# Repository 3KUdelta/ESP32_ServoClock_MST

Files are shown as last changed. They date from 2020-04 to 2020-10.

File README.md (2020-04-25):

# ESP32 ServoClock

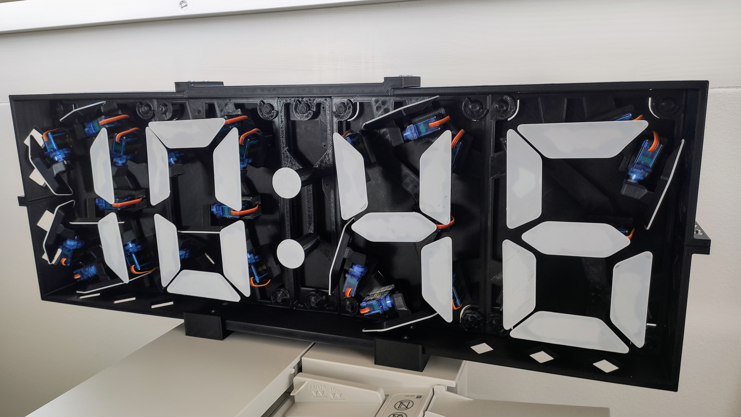
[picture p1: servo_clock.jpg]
ESP32 Servo Clock (https://github.com/3KUdelta/ESP32_ServoClock_MST)
\
Arduino code for digital clock, 3D printed inspired by www.otvinta.com, https://www.thingiverse.com/thing:3266949.
I added some thin back covers to hide the cables and added two feet to give a safe stand. These files are here: https://www.thingiverse.com/thing:4313748  

Author of the code: Jordi Ginjaume. Excellent code Jordi! It inspired me to do the thing with Arduino. Original Version 20190118 (his code and case can be found here: https://www.thingiverse.com/thing:3375870) 

Modified for use with an ESP32 wihtout RTC, just calling NTP all 12 hours over WiFi using the following hardware:

1 ESP32 programmed with Arduino\
2 PCA9685 chaining servo drivers, set solder blob on A0 on the second board for digits 3 and 4\
NTP call via WiFi\
28 SG90 servos

Important: keep sequence with servos plugging into PCA9685:\
first digit: 0-6, leave 7 blank\
second digit: 8-14, leave 15 blank\
repeat on second board for third and forth digit

PIN Connections on ESP32\
21 -- SLA\
22 -- SLC\
 0 -- OA
 
I inserted a switch to turn off the power to the PC9685 for programming purposes.

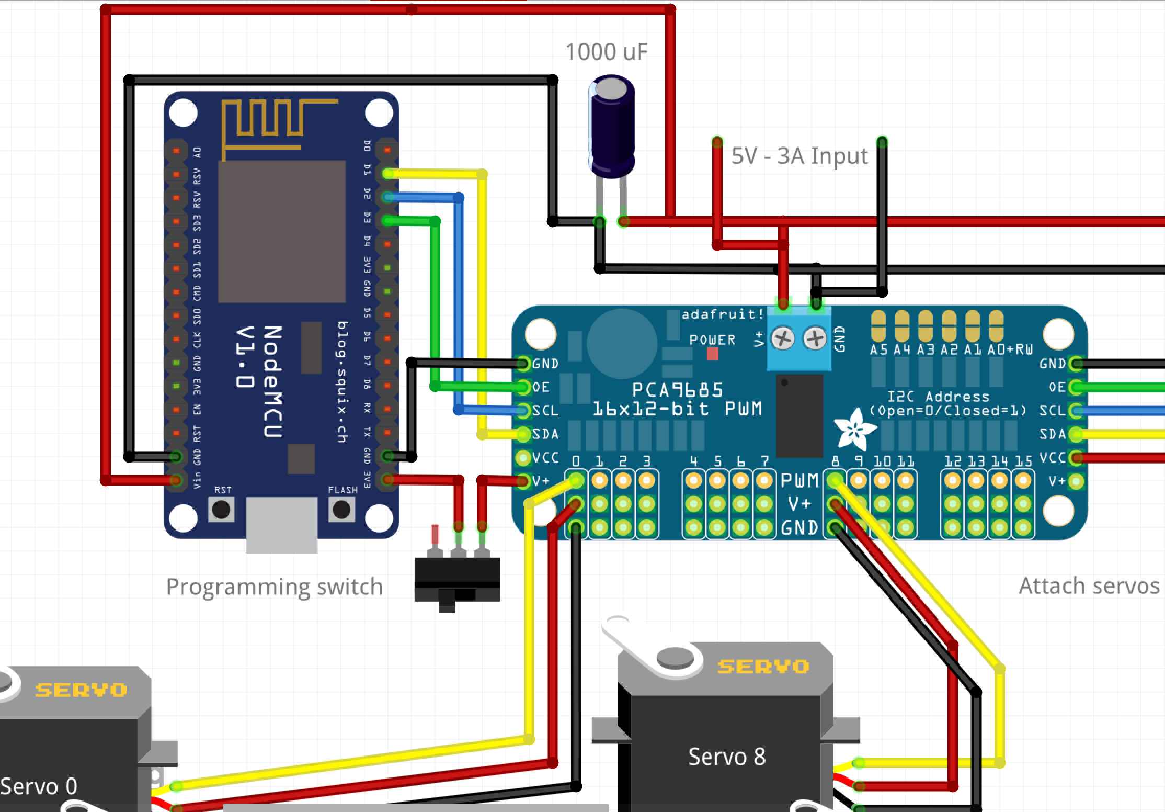
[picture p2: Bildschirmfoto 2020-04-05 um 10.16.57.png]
(https://github.com/3KUdelta/ESP32_ServoClock_MST)


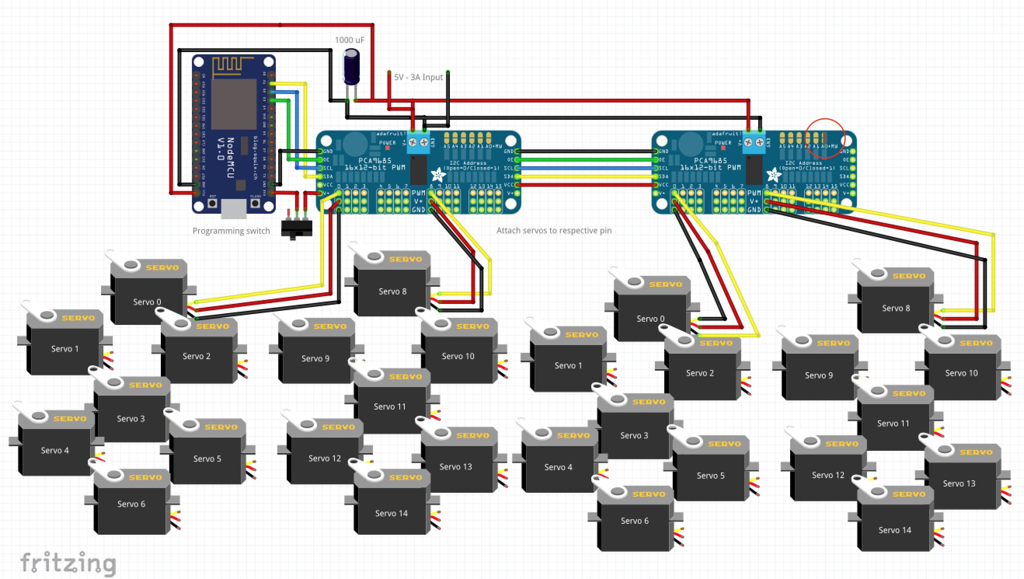
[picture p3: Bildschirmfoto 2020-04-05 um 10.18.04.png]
(https://github.com/3KUdelta/ESP32_ServoClock_MST)


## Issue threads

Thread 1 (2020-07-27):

Issues with Sketch

BzowK, 2020-07-27:
Good Morning!

I choose to use your build over the  as it's a cheaper option which seems to work just as well.  Unfortunately, I'm having two issues with your code...

## Issue 1 - 'resetFunc' was not declared in this scope ##

When attempting to verify just the original sketch you posted in IDE, I get the error above.  I added the following line above the function it's within and it verified afterwards.  Commenting out the line also verifies it, but sure it's there for a reason :)  Bringing it up as don't know if related to the 2nd issue.

    void(* resetFunc) (void) = 0; //declare reset function @ address 0

## Issue 2 - Sketch Not Working *(wdt reset)* ##
Once the above issue was addressed, I uploaded it to an NodeMCU and opened Serial Monitor.  Once up, the following was echoed and repeated every few seconds:

     ets Jan  8 2013,rst cause:4, boot mode:(3,6)
    wdt reset
    load 0x4010f000, len 1392, room 16
    tail 0
    chksum 0xd0
    csum 0xd0
    v3d128e5c
    ~ld

I've researched for at least an hour so far and found that its a watchdog reset, but don't know how to resolve it.  If it makes a difference, I have nothing connected to NodeMCU pins - it's just plugged into the PC via USB.  Some of the suggestions mention code issues, reducing long delays, & to pin assignments being incorrect.  Was hoping you could provide suggestions if not replicate.

*To note, the exact hardware I'm using is a KeeYees 3pcs ESP8266 NodeMCU CP2102 ESP-12E - a model I've never had issues with before and the pins match the ones in your diagram.*

Any suggestions or thoughts?  Thanks!

BzowK, 2020-07-27:
Think I got it working (I hope).  Basically replaced using the WiFi.h library with ESP8266WiFi.h then changed a couple other things to match.  Hopefully servo stuff works, too :)  Thanks

3KUdelta, 2020-07-27:
Hi, happy to see that it works.

Closed 2020-07-27.

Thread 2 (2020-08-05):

Servo Alignment / 12=00? / Wiring

BzowK, 2020-08-05:
Good Day, Again -

I've got two issues I've spent time trying to resolve without luck - hoping you can help...

**Servo Alignment**
So I finally got everything put together  and seemingly the sketch working, but when I powered it up, most of the segments (which I fortunately hadn't screwed in yet) went flying as it rotated them all over the place.  I added serial prints into part of the sketch so I could see which numbers it was trying to display, reattached the segments, then reset; but many went flying again :(  Not sure what the opening sequence is, but how do you suggest I proceed?

**12 Hour Clock**
I live in the US and (if I did it correctly) the serial prints are showing "00:45" for "12:45."  When not in a "12" hour, it outputs correctly.  Is there an easy code change to adjust this?  Note: The only changes I made to the time in the sketch were to define "TZ" as "6" and "UTC_OFFSET - TZ" to subtract 6 hours from the TZ as I'm Central time (US).  Here's my current sketch minus SSID/Password...
[ServoClockGen.ino.txt](https://github.com/3KUdelta/ESP32_ServoClock_MST/files/5030179/ServoClockGen.ino.txt)

**Wiring**
When initially hooking everything up, I couldn't get it to work at all.  I eventually found this post that the SCL & SDA wires should be hooked up in reverse to what your diagram showed.  Once I swapped them, it started to (theoretically) work.  I made a new Fritzing image which I pasted below as an example of what worked for me.

Any suggestions would be appreciated - Thanks!

**UPDATE**
I think I got the first one set where I can get the segments close to correct.  Not sure in sketch how to fine tune each, though.

3KUdelta, 2020-08-08:
Hi
I hope I can help you with your questions:
Servo Alignment, please use this part of the code:
`const int servofinetune [4] [7] = {      // pulse to add to servopulse for fine tunning of each individual servo
  { -25, 0, 0, 10, -30, 0, -20},
  {0, -20, 0, -10, -55, -5, 30},
  {0, -20, -15, 0, 0, 0, 0},
  {20, 20, -10, 0, 10, -10, 10}
};`

Each group represents one digit with the corresponding 7 servos. E.g. {servo0, servo1, ... }. The initial sequence puts all servos to ON. Then unplug the power. Observe the state of the servos and put a correction factor for each servo. For my build I had to correct the first servo -25. It was overshooting. You need to try this out a several times.

Time Zone and 12 hour display:
Unfortunately for you,  the code was built for European usage and automatic calculation of DST for Europe. The settings for your time zone in general are fine. The DST is an extra calculation. Therefore your changes need to consider exchanging the rules for the daylight saving time for your region. This code at the end needs to be adjusted to your rules:
` boolean summertime_EU(int year, byte month, byte day, byte hour, byte tzHours)
// European Daylight Savings Time calculation by "jurs" for German Arduino Forum
// input parameters: "normal time" for year, month, day, hour and tzHours (0=UTC, 1=MEZ)
// return value: returns true during Daylight Saving Time, false otherwise
{
  if (month < 3 || month > 10) return false; // no changes in Jan, Feb, Nov, Dec
  if (month > 3 && month < 10) return true;  // changes in Apr, May, Jun, Jul, Aug, Sep
  if (month == 3 && (hour + 24 * day) >= (1 + tzHours + 24 * (31 - (5 * year / 4 + 4) % 7)) || month == 10 && (hour + 24 * day) < (1 + tzHours + 24 * (31 - (5 * year / 4 + 1) % 7)))
    return true;
  else
    return false;
} // end of summertime_EU()`

If you want to change the 24 hour display to 12 hour you need to deduct 12 hours if time larger than 11.
This should work at the end of the function void get_NTP_time():
If (hour(now()) >=12) adjustTime(-43200); // 43200 seconds = 12 hours

The wiring should be as indicated in the text. The picture might be misleading.
    PIN Connections on ESP32
    21 -- SLA
    22 -- SLC
     0 -- OA

Hope this helps.

BzowK, 2020-08-28:
Really appreciate your reply.  Just updated sketch and going to work on it this weekend.  Closing out this issue - hoping it doesn't jinx me :)

Thanks

Closed 2020-08-28.

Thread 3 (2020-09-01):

Servo Limits

BzowK, 2020-09-01:
Hey -

I'm sorry to bother again, but have one final issue I cannot figure out for the life of me.  I've got the panels fine tuned as best possible, however; when some of them are off, I can hear a few of the servos seizing as their panels have hit the frame.  Adjusting them via finetuning so they do not do this has them go out of alignment and I'm certain they are seated correctly so am trying to set the global "off" position.

I tried adjusting the "210" & "450" values of "const int servopulse [2] {210, 450};" yet doing so affects the reverse servos in the opposite direction as desired.  Is this a code change that can easily be achieved by only changing a couple of values?

Thanks again!

3KUdelta, 2020-09-01:
Hi,
I am not sure that the problem lays in the software. I assume a hardware issue. Please check these things: 1.) do you provide enough power? You need at least 3 amps. 2.) do you power the PCA9685 over the power plug on top and not over the solder points? 3.) are you using en ESP32? I had trouble using an ESP8266. 4.) Are the cables properly soldered (connected)? 5.) avoid taking 5 v from the ESP - simply follow exactly the drawing.
Hope this helps.

BzowK, 2020-09-02:
Thanks for the reply...

Below are answers, but I don't believe it's pwoer-related.  It's not that the servos don't have enough power - they do.  It's that when some rotate into the off position (especially the bottom for each #), their attached "segment" hits the frame preventing it from reaching it's desired position.  When this occurs, the servo keeps trying to move it there, but can't therefore causing the buzz and making the servo get hot over time.

Hope that explains it.  Below is the answer for each question just in case.  Thanks!

1. Yes - 5V 3A source (via UBEC)
2. Correct - the top of each PCA9685 is connected directly to the 5V 3A
3. I'm using a NodeMCU ESP-12E which is fed via 5V 3A + capacitor as suggested in your diagram
4. Yes - everything is soldered
5. I did the diagram exactly power-wise

3KUdelta, 2020-09-03:
Good to read that it is not power related. I woiuld help a great deal if you could send a link to a video to better understand what is happening.

BzowK, 2020-09-04:
Hello -

Thanks again for your reply and willingness to assist.  I took a video a few minutes ago which is linked below.  Once the panels turn off, you should be able to hear the buzzing from the servos.  At the end of the video I go up close to the bottom (G) one of the first digit where you can see the panel hitting the frame which blocks the rotation and causes the buzzing.  This seems to affect most if not all panels on the top (A) & bottom (G).  You may notice these panels misaligned when all are on - this is because I've been trying to fine-tune them so they won't hit the frame without success.
[https://photos.app.goo.gl/JWaNE2e1TMyQ16pVA](https://photos.app.goo.gl/JWaNE2e1TMyQ16pVA)

Below is my current sketch.  The only changes should be from me testing things, adding in code to convert to a 12-hour clock, & code to display the hour to be "12" when reported as "00".
[https://kellermannnetwork.com/owncloud/s/lAuKBkuCU0jOKZB](https://kellermannnetwork.com/owncloud/s/lAuKBkuCU0jOKZB)

Hope that helps - any suggestions?  Thanks again!

3KUdelta, 2020-09-04:
One thing I can spot immediately. The middle servos are in the wrong "park" positions. If they are not showing the bar they are supposed to go downwards. Yours are going upwards.

BzowK, 2020-09-04:
Hmm - That's odd. Just looked and none of them are surging / hitting the frame unfortunately...

3KUdelta, 2020-09-05:
OK, got some time to go through your things.
Just tweak the following line and you should be ok:
`const int servopulse [2] {210, 450};      // pulse of servos at low positions and high position`
The values 210 and 450 gives the two different up and down states. So you might change 450 to 430 or less to get rid of your problem.

BzowK, 2020-09-07:
Good Day -

Thanks again.  Will try out in a bit and let you know results.  Still wondering why middle servos are flipping opposite from yours, too.  If nogo, may start fresh from you uploaded sketch again and see results.

Thanks

3KUdelta, 2020-09-07:
Hi, I don't think that matters a lot. As long as the individual servos are not blocking each other.
You can change this here:
`const byte servoreverse [4] [7] = {      // one identifies wservos that work reverse, zero is normal direction
  {1, 1, 0, 0, 0, 1, 1},
  {1, 1, 0, 0, 0, 1, 1},
  {1, 1, 0, 0, 0, 1, 1},
  {1, 1, 0, 0, 0, 1, 1}
};`
First things first - change the high/low positions and you will be fine...

BzowK, 2020-09-08:
Good Day -

Think that did it!  I changed it to "400".  Could have sworn I tried that previously, but have probably tried well over 100 sketch modifications so may had missed something in the past or more than likely not adjusted it enough.  Thanks!

To note, there are still two things I had to do initially from your code to get things working in case you wish to update them...

- I compared my sketch with the one you have posted and remembered that initially it wouldn't even compile without adding a lines.  Prior to the "void get_NTP_time() {" line, I had to add "void(* resetFunc) (void) = 0; //declare reset function @ address 0
" else it wouldn't compile
- I also had to swap the SLA / SLC from how you had them wired in the diagram.

Just notes in case you wish to change.  Thanks again for your help!

Closed 2020-09-08.

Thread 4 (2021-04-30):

12 Hour Clock Question / Null 1st Digit

BzowK, 2021-04-30:
Hey!

Had to put project aside for a while, but finished it up recently and love it.  Thanks a lot for taking time to code the way you did.  I did have an issue, a question, & a suggestion I've been meaning to post about, though.  Any assistance would be greatly appreciated...

**The Issue**
Time Correctly Sets to a 12 Hour clock if powered on in PM hours.  If powered on in AM hours, it shows 24 hour clock after noon.  Resetting power shows time with 12 hour clock again as it should.
_In other words, if powered on in the AM, once it's 1:00pm, it shows 13:00.  Cycling the power (correctly) shows it is 1:00_

I have the below line at the end of the  get_NTP_time function but seemingly only runs it once when powered on.  Looks to me like it should be in the loop, but no coding expert :)

> if (hour(now()) >=12) adjustTime(-43200); // 43200 seconds = 12 hours

_...Entire code below..._

**The Question**
Since I use a 12 hour clock, I obviously only use the first digit / 8 servos for the occasional "1".  I've tried editing the code to make the first digit display nothing (all servos in off position) instead of a "0" when the time not "11" or "12", but have so far been unsuccessful.  Would this be an easy change or no?

**The Suggestion**
My clock required a lot of fine-tuning which obviously requires removing from wall, disconnecting the power from the servo boards (I put a switch in as suggested), etc.  I instead added in code to use OTA to perform flashes which works great.  If you'd like to add (or not), I've attached my current sketch.

Any suggestions would be appreciated - Thanks!

```
#include <Wire.h>
#include <Adafruit_PWMServoDriver.h>
#include <ESP8266WiFi.h>
#include <WiFiUdp.h>
#include <EasyNTPClient.h>
#include <TimeLib.h>
#include <ESP8266mDNS.h>
#include <ArduinoOTA.h>

// WiFi
#define STASSID "YourWifiSSID"  // Insert wifi SSID here
#define STAPSK  "WifiPassword"   // Insert wifi password here
const char* ssid     = STASSID;
const char* password = STAPSK;

// NTP
#define NTP_SERVER   "ch.pool.ntp.org"
#define TZ           -6
#define TZ_SEC       ((TZ)*3600)
#define UTC_OFFSET + TZ

Adafruit_PWMServoDriver servoHours = Adafruit_PWMServoDriver(0x40);   //first PCA9685 address
Adafruit_PWMServoDriver servoMinutes = Adafruit_PWMServoDriver(0x41); //second PCA9685 address, solder blob on A0

WiFiUDP udp;
EasyNTPClient ntpClient(udp, NTP_SERVER, TZ_SEC);  //calls NTP for current timezone; summertime_EU() does the rest

//*** declaration of functions ***************************************************

void capturetime();
void showtime(byte m [4], int w);
void showdigit(byte i, byte digit, int w);
void go_online();
void get_NTP_time();
boolean summertime_EU(int year, byte month, byte day, byte hour, byte tzHours);

//*********************************************************************************

const int enablepin = 0;                  // ESP32 pin connected to the OE pin at PCA9685, would also work without
const int servopulse [2] {210, 400};      // pulse of servos at low positions and high position

const byte mapchar [12][7] = { //for each number, position of every segment
  {1, 1, 1, 0, 1, 1, 1}, // zero          //   0
  {0, 0, 1, 0, 0, 1, 0}, // one           // 1   2
  {1, 0, 1, 1, 1, 0, 1}, // two           //   3
  {1, 0, 1, 1, 0, 1, 1}, // three         // 4   5
  {0, 1, 1, 1, 0, 1, 0}, // four          //   6
  {1, 1, 0, 1, 0, 1, 1}, // five
  {1, 1, 0, 1, 1, 1, 1}, // six
  {1, 0, 1, 0, 0, 1, 0}, // seven
  {1, 1, 1, 1, 1, 1, 1}, // eight
  {1, 1, 1, 1, 0, 1, 1}, // nine
  {0, 0, 0, 0, 0, 0, 0}, // null (all down)
  {1, 1, 0, 1, 1, 0, 1}  // E for error indication
};

const byte servoreverse [4] [7] = {      // one identifies wservos that work reverse, zero is normal direction
  {1, 1, 0, 0, 0, 1, 1},
  {1, 1, 0, 0, 0, 1, 1},
  {1, 1, 0, 0, 0, 1, 1},
  {1, 1, 0, 0, 0, 1, 1}
};
const int servofinetune [4] [7] = {      // pulse to add to servopulse for fine tunning of each individual servo
  //positive increase adjusts to the right
 // 0, 1, 2, 3, 4, 5, 6
  {0, 0, 30, 20, 35, -30, 10},
 //7, 8, 9, 10, 11, 12, 13
  {-5, 40, 40, 25, 60, 5, 30},
 //14, 15, 16, 17, 18, 19, 20
  {-20, 40, 40, 55, 65, .5, -15},
 //21, 22, 23, 24, 25, 26, 27
  {-35, 30, 35, 15, 35, 10, 15},
};
byte allon [4] = {8, 8, 8, 8};           // all digits on
byte alloff [4] = {10, 10, 10, 10};      // all digits off for startup
byte momentdisplay [4];                  // time shown in display
byte moment [4];                         // to store actual time in 4 digits
unsigned long timestamp;                 // timestamp to measure time past since last update on NTP server

void setup() {
  delay(500);                            // give time after boot
  Serial.begin(115200);
  Serial.println();
  Serial.println();
  Serial.print("Connecting to ");
  Serial.println(ssid);
  pinMode(enablepin, OUTPUT);            // this is the pin for OE in the PCA (enable/disable servos LOW/HIGH)
  servoHours.begin();
  servoHours.setPWMFreq(50);             // set frequncy for first PCA
  servoMinutes.begin();
  servoMinutes.setPWMFreq(50);           // set frequency for second PCA
  digitalWrite(enablepin, LOW);          // enable the servos
  delay(200);
  showtime(allon, 220);                  // initializing all servos
  showtime(alloff, 220);
  go_online();                           // connect to WiFi
  get_NTP_time();                        // get precise time from time server

  ArduinoOTA.setHostname("ServoClock");
  ArduinoOTA.onStart([]() {
    String type;
    if (ArduinoOTA.getCommand() == U_FLASH)
      type = "sketch";
    else // U_SPIFFS
      type = "filesystem";

    // NOTE: if updating SPIFFS this would be the place to unmount SPIFFS using SPIFFS.end()
    Serial.println("Start updating " + type);
  });
  ArduinoOTA.onEnd([]() {
    Serial.println("\nEnd");
    ESP.restart();
  });
  ArduinoOTA.onProgress([](unsigned int progress, unsigned int total) {
    Serial.printf("Progress: %u%%\r", (progress / (total / 100)));
  });
  ArduinoOTA.onError([](ota_error_t error) {
    Serial.printf("Error[%u]: ", error);
    if (error == OTA_AUTH_ERROR) Serial.println("Auth Failed");
    else if (error == OTA_BEGIN_ERROR) Serial.println("Begin Failed");
    else if (error == OTA_CONNECT_ERROR) Serial.println("Connect Failed");
    else if (error == OTA_RECEIVE_ERROR) Serial.println("Receive Failed");
    else if (error == OTA_END_ERROR) Serial.println("End Failed");
  });
  ArduinoOTA.begin();
//  Serial.println("Ready");
//  Serial.print("IP address: ");
//  Serial.println(WiFi.localIP());
}

void loop() {
  capturetime();                         // assign time to digits
  showtime(moment, 220);                 // to the main routine that shows the time in our digital clock
  if ((now() - timestamp) > 43200) {     // 43200 = 12 hours
    get_NTP_time();                      // get all 12 hours a time update from NTP Server --> avoiding a constant read from time server
  }
  ArduinoOTA.handle();
}

void capturetime() {
  moment[0] = hour(now()) / 10;               // find out first digit from hour
  moment[1] = hour(now()) - moment[0] * 10;   // find out second digit from hour
  moment[2] = minute(now()) / 10;             // find our first digit from minute
  moment[3] = minute(now()) - moment[2] * 10; // find out second digit from minute
  if ((hour(now()) < 1)) { // if hour is "0", displays a "12"
    moment[0] = 1;       
    moment[1] = 2;
  }
// Serial.println();
Serial.println(moment[0]);
Serial.println(moment[1]);
Serial.println(moment[2]);
Serial.println(moment[3]);
Serial.println();
Serial.println(hour(now()));
//Serial.println(minute(now()));
}

void showtime(byte m [4], int w) {
  int d = 275; // delay needed to stop the servos moving before disabling them
  // parameters: matrix with the digits to show
  if (memcmp(m, momentdisplay, 4) != 0) { // if time displayed is different to time expected to be shown
    for (int i = 0; i < 4; i++) { // for every single position, show only if different to actually shown
      if (m[i] != momentdisplay[i]) {
        showdigit(i, m[i], w);
        momentdisplay [i] = m[i]; // take note of the shown digit
      }
    }
    delay(d); // give time to the servos to stop moving
  }
  }

void showdigit(byte i, byte digit, int w) { // parameters: i = digit position (0,1,2,3), digit = number, w = delay avoiding high power draw
  int pulse;
  byte servonum, a, segmentposition;

  for (byte j = 0; j < 7; j++) { // show the 7 segments
    servonum = j + (8 * ((i == 1 || i == 3))); // add 8 if position is 1 or 3 because 1 ands 3 digits start on pin 8 of the PCA
    segmentposition = mapchar[digit] [j]; // segment should be low or high?
    if (servoreverse [i] [j] == 0) {
      pulse = servopulse[segmentposition]; // for a normal (not reverse) servo assign pulse low or high
    }
    else {
      pulse = servopulse[!segmentposition]; // if servo works reverse, assign contrary
    }
    pulse = pulse + servofinetune [i] [j]; // add the fine tunning to the servo

    switch (i) { // switch for both PCA controllers
      case 0: case 1:
        servoHours.setPWM(servonum, 0, pulse);
        break;
      case 2: case 3:
        servoMinutes.setPWM(servonum, 0, pulse);
        break;
    }
    delay(w); // delay in between movement of contiguous segments, so we can do waves oleeeeeeee.
  }
}

void go_online() {
  WiFi.mode(WIFI_STA);
  WiFi.begin(ssid, password);
  Serial.print("---> Connecting to WiFi ");
  int i = 0;
  while (WiFi.status() != WL_CONNECTED) {
    delay(500);
    i++;
    if (i > 20) {
      Serial.println("Could not connect to WiFi!");
      Serial.println("Doing a reset now and retry a connection from scratch.");
      showdigit(0, 11, 100);                  // E
      showdigit(2, 0, 100);                   // 0
      showdigit(3, 1, 100);                   // 1 : shows Error 01, could not connect to WiFi
      delay(5000);                            // wait 5 secs and then do a retry
      showtime(alloff, 220);
      go_online();                            // try again
    }
    Serial.print(".");
  }
  Serial.println("Wifi connected ok.");
} //end go_online

void(* resetFunc) (void) = 0; //declare reset function @ address 0

void get_NTP_time() {
  Serial.println("---> Now reading time from NTP Server");
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
3KUdelta, 2021-05-01:
Hi, let's see if I can help.
**For your issue:**
just MOVE the line
`if (hour(now()) >=12) adjustTime(-43200); // 43200 seconds = 12 hours`
as the first instruction in function void capturetime(). Like this:
```
void capturetime() {
if (hour(now()) >=12) adjustTime(-43200); // 43200 seconds = 12 hours
moment[0] = hour(now()) / 10;               // find out first digit from hour
```
This should do it. Unfortunately, I cannot test on my installation.

**For your question:**

I don't get this:
```
  if ((hour(now()) < 1)) { // if hour is "0", displays a "12"
    moment[0] = 1;       
    moment[1] = 2;
  }
```
exchange it with these lines an the leading zero should dissapear
```
if (hour(now()) < 10) {  // if leading zero
moment[0] = 10;  // 10 is defined as all servos down
}
```

**For your suggestion:**

I like the idea of the OTA approach. Please use the "Fork" function on the top right in GitHub to generate your own fork to share an maintain you own code.

Hope this works. Marc

BzowK, 2021-05-03:
Thanks so much for your reply and assistance!

I'll give the code a shot tomorrow and let you know the results.  Will start a fork as well in case it helps anyone else.  Thanks again for the help!

BzowK, 2021-05-03:
Both solutions worked like a champ - Thanks again!!

3KUdelta, 2021-05-03:
You're welcome.

Closed 2021-05-03.

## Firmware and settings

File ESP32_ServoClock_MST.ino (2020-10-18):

/*
    Digital Clock
    Jordi Ginjaume
    Version 20190118
    Code started 20190110

    Arduino code for digital clock, 3D printed inspired by www.otvinta.com, using the following hardware:
    1 Arduino ESP32
    2 PCA9685 chaining servo drivers, set solder blob on A0 on the second board for digits 3 and 4
    NTP call via WiFi
    28 SG90 servos

    Modified for use with an ESP32 wihtout RTC, just calling NTP all 12 hours over WiFi
    Marc Stähli, modified April 2020

    Important: keep sequence with servos plugging into PCA9685:
    first digit: 0-6, leave 7 blank
    second digit: 8-14, leave 15 blank
    repeat on second board for third and forth digit
    Sequece per digit:   0
                       1   2
                         3
                       4   5
                         6

    PIN Connections on ESP32
    21 -- SLA
    22 -- SLC
     0 -- OA
*/

#include <Wire.h>
#include <Adafruit_PWMServoDriver.h>    // Adafruit PCA9685 library
#include <WiFi.h>                       // For WiFi connection with ESP32
#include <WiFiUdp.h>                    // For NTP Signal fetch
#include <EasyNTPClient.h>              // For NTP Signal read https://github.com/aharshac/EasyNTPClient
#include <TimeLib.h>                    // For converting NTP time https://github.com/PaulStoffregen/Time.git

char ssid[] = "eiger1";                 // WiFi Router ssid
char pass[] = "Beloc-Zok-0123456789";   // WiFi Router password

// NTP
#define NTP_SERVER   "ch.pool.ntp.org"
#define TZ           1                  // (utc+) TZ in hours
#define TZ_SEC       ((TZ)*3600)        // remark: European DST will be calculated in the code
#define UTC_OFFSET + TZ

Adafruit_PWMServoDriver servoHours = Adafruit_PWMServoDriver(0x40);   //first PCA9685 address
Adafruit_PWMServoDriver servoMinutes = Adafruit_PWMServoDriver(0x41); //second PCA9685 address, solder blob on A0

WiFiUDP udp;
EasyNTPClient ntpClient(udp, NTP_SERVER, TZ_SEC);  //calls NTP for current timezone; summertime_EU() does the rest

//*** declaration of functions ***************************************************

void capturetime();
void showtime(byte m [4], int w);
void showdigit(byte i, byte digit, int w);
void go_online();
void get_NTP_time();
boolean summertime_EU(int year, byte month, byte day, byte hour, byte tzHours);
void(* resetFunc) (void) = 0;       // declare reset function @ address 0

//*********************************************************************************

const int enablepin = 0;                  // ESP32 pin connected to the OE pin at PCA9685, would also work without
const int servopulse [2] {210, 450};      // pulse of servos at low positions and high position

const byte mapchar [12][7] = { //for each number, position of every segment
  {1, 1, 1, 0, 1, 1, 1}, // zero          //   0
  {0, 0, 1, 0, 0, 1, 0}, // one           // 1   2
  {1, 0, 1, 1, 1, 0, 1}, // two           //   3
  {1, 0, 1, 1, 0, 1, 1}, // three         // 4   5
  {0, 1, 1, 1, 0, 1, 0}, // four          //   6
  {1, 1, 0, 1, 0, 1, 1}, // five
  {1, 1, 0, 1, 1, 1, 1}, // six
  {1, 0, 1, 0, 0, 1, 0}, // seven
  {1, 1, 1, 1, 1, 1, 1}, // eight
  {1, 1, 1, 1, 0, 1, 1}, // nine
  {0, 0, 0, 0, 0, 0, 0}, // null (all down)
  {1, 1, 0, 1, 1, 0, 1}  // E for error indication
};

const byte servoreverse [4] [7] = {      // one identifies wservos that work reverse, zero is normal direction
  {1, 1, 0, 0, 0, 1, 1},
  {1, 1, 0, 0, 0, 1, 1},
  {1, 1, 0, 0, 0, 1, 1},
  {1, 1, 0, 0, 0, 1, 1}
};
const int servofinetune [4] [7] = {      // pulse to add to servopulse for fine tunning of each individual servo
  { -25, 0, 0, 10, -30, 0, -20},
  {0, -20, 0, -10, -55, -5, 30},
  {0, -20, -15, 0, 0, 0, 0},
  {20, 20, -10, 0, 10, -10, 10}
};
byte allon [4] = {8, 8, 8, 8};           // all digits on
byte alloff [4] = {10, 10, 10, 10};      // all digits off for startup
byte momentdisplay [4];                  // time shown in display
byte moment [4];                         // to store actual time in 4 digits
unsigned long timestamp;                 // timestamp to measure time past since last update on NTP server

void setup() {
  delay(500);                            // give time after boot
  Serial.begin(115200);
  pinMode(enablepin, OUTPUT);            // this is the pin for OE in the PCA (enable/disable servos LOW/HIGH)
  servoHours.begin();
  servoHours.setPWMFreq(60);             // set frequncy for first PCA
  servoMinutes.begin();
  servoMinutes.setPWMFreq(60);           // set frequency for second PCA
  digitalWrite(enablepin, LOW);          // enable the servos
  delay(200);
  showtime(allon, 220);                  // initializing all servos
  showtime(alloff, 220);
  go_online();                           // connect to WiFi
  get_NTP_time();                        // get precise time from time server
}

void loop() {
  capturetime();                         // assign time to digits
  showtime(moment, 220);                 // to the main routine that shows the time in our digital clock
  if ((now() - timestamp) > 43200) {     // 43200 = 12 hours
    get_NTP_time();                      // get all 12 hours a time update from NTP Server --> avoiding a constant read from time server
  }
}

void capturetime() {
  moment[0] = hour(now()) / 10;               // find out first digit from hour
  moment[1] = hour(now()) - moment[0] * 10;   // find out second digit from hour
  moment[2] = minute(now()) / 10;             // find our first digit from minute
  moment[3] = minute(now()) - moment[2] * 10; // find out second digit from minute
}

void showtime(byte m [4], int w) {
  int d = 275; // delay needed to stop the servos moving before disabling them
  // parameters: matrix with the digits to show
  if (memcmp(m, momentdisplay, 4) != 0) { // if time displayed is different to time expected to be shown
    for (int i = 0; i < 4; i++) { // for every single position, show only if different to actually shown
      if (m[i] != momentdisplay[i]) {
        showdigit(i, m[i], w);
        momentdisplay [i] = m[i]; // take note of the shown digit
      }
    }
    delay(d); // give time to the servos to stop moving
  }
}

void showdigit(byte i, byte digit, int w) { // parameters: i = digit position (0,1,2,3), digit = number, w = delay avoiding high power draw
  int pulse;
  byte servonum, a, segmentposition;

  for (byte j = 0; j < 7; j++) { // show the 7 segments
    servonum = j + (8 * ((i == 1 || i == 3))); // add 8 if position is 1 or 3 because 1 ands 3 digits start on pin 8 of the PCA
    segmentposition = mapchar[digit] [j]; // segment should be low or high?
    if (servoreverse [i] [j] == 0) {
      pulse = servopulse[segmentposition]; // for a normal (not reverse) servo assign pulse low or high
    }
    else {
      pulse = servopulse[!segmentposition]; // if servo works reverse, assign contrary
    }
    pulse = pulse + servofinetune [i] [j]; // add the fine tunning to the servo

    switch (i) { // switch for both PCA controllers
      case 0: case 1:
        servoHours.setPWM(servonum, 0, pulse);
        break;
      case 2: case 3:
        servoMinutes.setPWM(servonum, 0, pulse);
        break;
    }
    delay(w); // delay in between movement of contiguous segments, so we can do waves oleeeeeeee.
  }
}

void go_online() {
  WiFi.mode(WIFI_STA);
  WiFi.begin(ssid, pass);
  Serial.print("---> Connecting to WiFi ");
  int i = 0;
  while (WiFi.status() != WL_CONNECTED) {
    delay(500);
    i++;
    if (i > 20) {
      Serial.println("Could not connect to WiFi!");
      Serial.println("Doing a reset now and retry a connection from scratch.");
      showdigit(0, 11, 100);                  // E
      showdigit(2, 0, 100);                   // 0
      showdigit(3, 1, 100);                   // 1 : shows Error 01, could not connect to WiFi
      delay(5000);                            // wait 5 secs and then do a retry
      showtime(alloff, 220);
      go_online();                            // try again
    }
    Serial.print(".");
  }
  Serial.println("Wifi connected ok.");
} //end go_online

void get_NTP_time() {
  Serial.println("---> Now reading time from NTP Server");
  
  if (WiFi.status() != WL_CONNECTED) {
    Serial.println("WiFi not connected! Doing that now again.");
    go_online();
  }
  int i = 0;
  while (!ntpClient.getUnixTime()) {
    delay(500);
    i++;
    if (i > 20) {
      Serial.println("Could not connect to NTP server!");
      Serial.println("Doing a reset now and retry a connection from scratch.");
      showdigit(0, 11, 100);                  // E
      showdigit(2, 0, 100);                   // 0
      showdigit(3, 2, 100);                   // 2 : shows Error 02, could not connect to NTP server
      delay(5000);                            // wait 5 secs and then do a reset
      resetFunc();                            // doing a full reset to retry
    }
    Serial.print(".");
  }

  setTime(ntpClient.getUnixTime());           // get UNIX timestamp (seconds from 1.1.1970 on)

  if (summertime_EU(year(now()), month(now()), day(now()), hour(now()), 1)) {
    adjustTime(3600);                         // adding one hour
  }
  timestamp = now();
} // end get_NTP_time()

boolean summertime_EU(int year, byte month, byte day, byte hour, byte tzHours)
// European Daylight Savings Time calculation by "jurs" for German Arduino Forum
// input parameters: "normal time" for year, month, day, hour and tzHours (0=UTC, 1=MEZ)
// return value: returns true during Daylight Saving Time, false otherwise
{
  if (month < 3 || month > 10) return false; // keine Sommerzeit in Jan, Feb, Nov, Dez
  if (month > 3 && month < 10) return true;  // Sommerzeit in Apr, Mai, Jun, Jul, Aug, Sep
  if (month == 3 && (hour + 24 * day) >= (1 + tzHours + 24 * (31 - (5 * year / 4 + 4) % 7)) || month == 10 && (hour + 24 * day) < (1 + tzHours + 24 * (31 - (5 * year / 4 + 1) % 7)))
    return true;
  else
    return false;
} // end of summertime_EU()
